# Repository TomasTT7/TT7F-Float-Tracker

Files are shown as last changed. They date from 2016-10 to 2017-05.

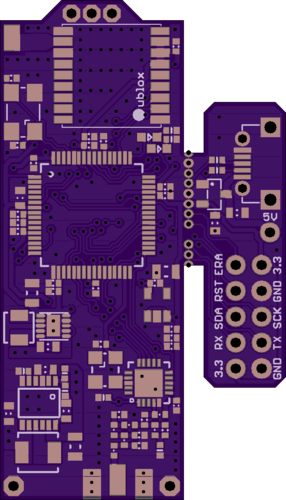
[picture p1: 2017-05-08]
Hardware/TT7F v1.5 top.png

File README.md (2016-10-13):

# TT7F-Float-Tracker

This is the main repository for [TT7F high altitude balloon tracker](http://tt7hab.blogspot.cz/2016/08/the-tt7f-hardware.html).
It includes the board and schematic Eagle files and the current state of software that is continually being worked on.

The tracker is designed around Atmel's SAM3S8B microcontroller. It acquires the current position from Ublox MAX-M8Q GPS module. As a transmitter it uses Silicon Labs Si4060 to transmit in the 70cm and 2m bands. It is also equipped with a connector and an interface for MT9D111 camera module to provide [SSDV](https://ukhas.org.uk/guides:ssdv) (Slow Scan Digital Video) capability.

The power supply consists of TPS63031 buck-boost converter providing 3.3V to the MCU, GPS module and transmitter. The MT9D111 camera module is powered by two ME6211 LDO regulators (1.8V and 2.8V). The tracker is also capable of using LTC3105 MPPC converter in connection with a pair of solar cells to charge a battery (up to 4.2V) and power the TPS63031 converter.

For programming purposes it is equipped with a USB micro B interface which can provide power to the board via MCP1700 LDO regulator as well.

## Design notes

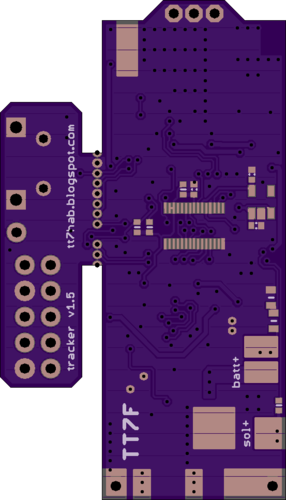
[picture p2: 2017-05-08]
Hardware/TT7F v1.5 bottom.png

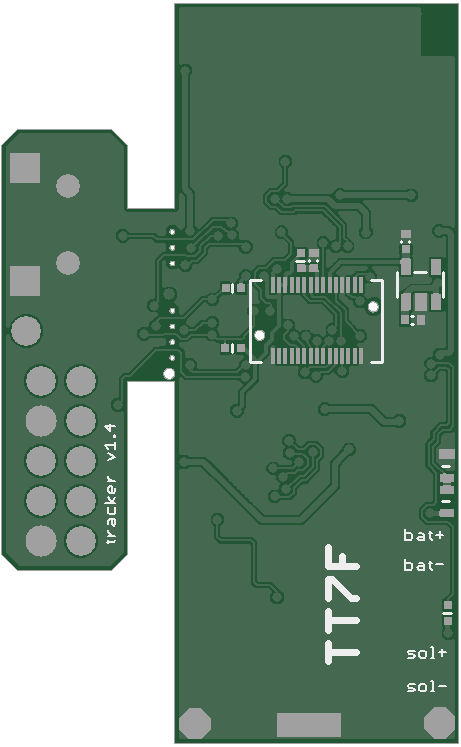
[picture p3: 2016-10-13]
Hardware/PCB bottom.png

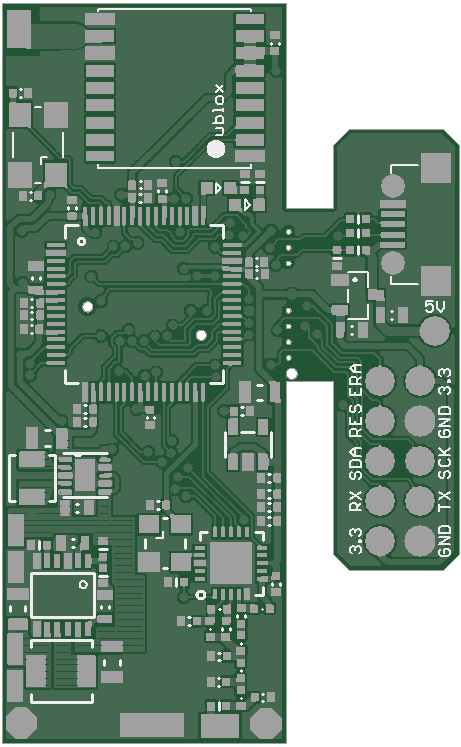
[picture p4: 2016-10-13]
Hardware/PCB top.png

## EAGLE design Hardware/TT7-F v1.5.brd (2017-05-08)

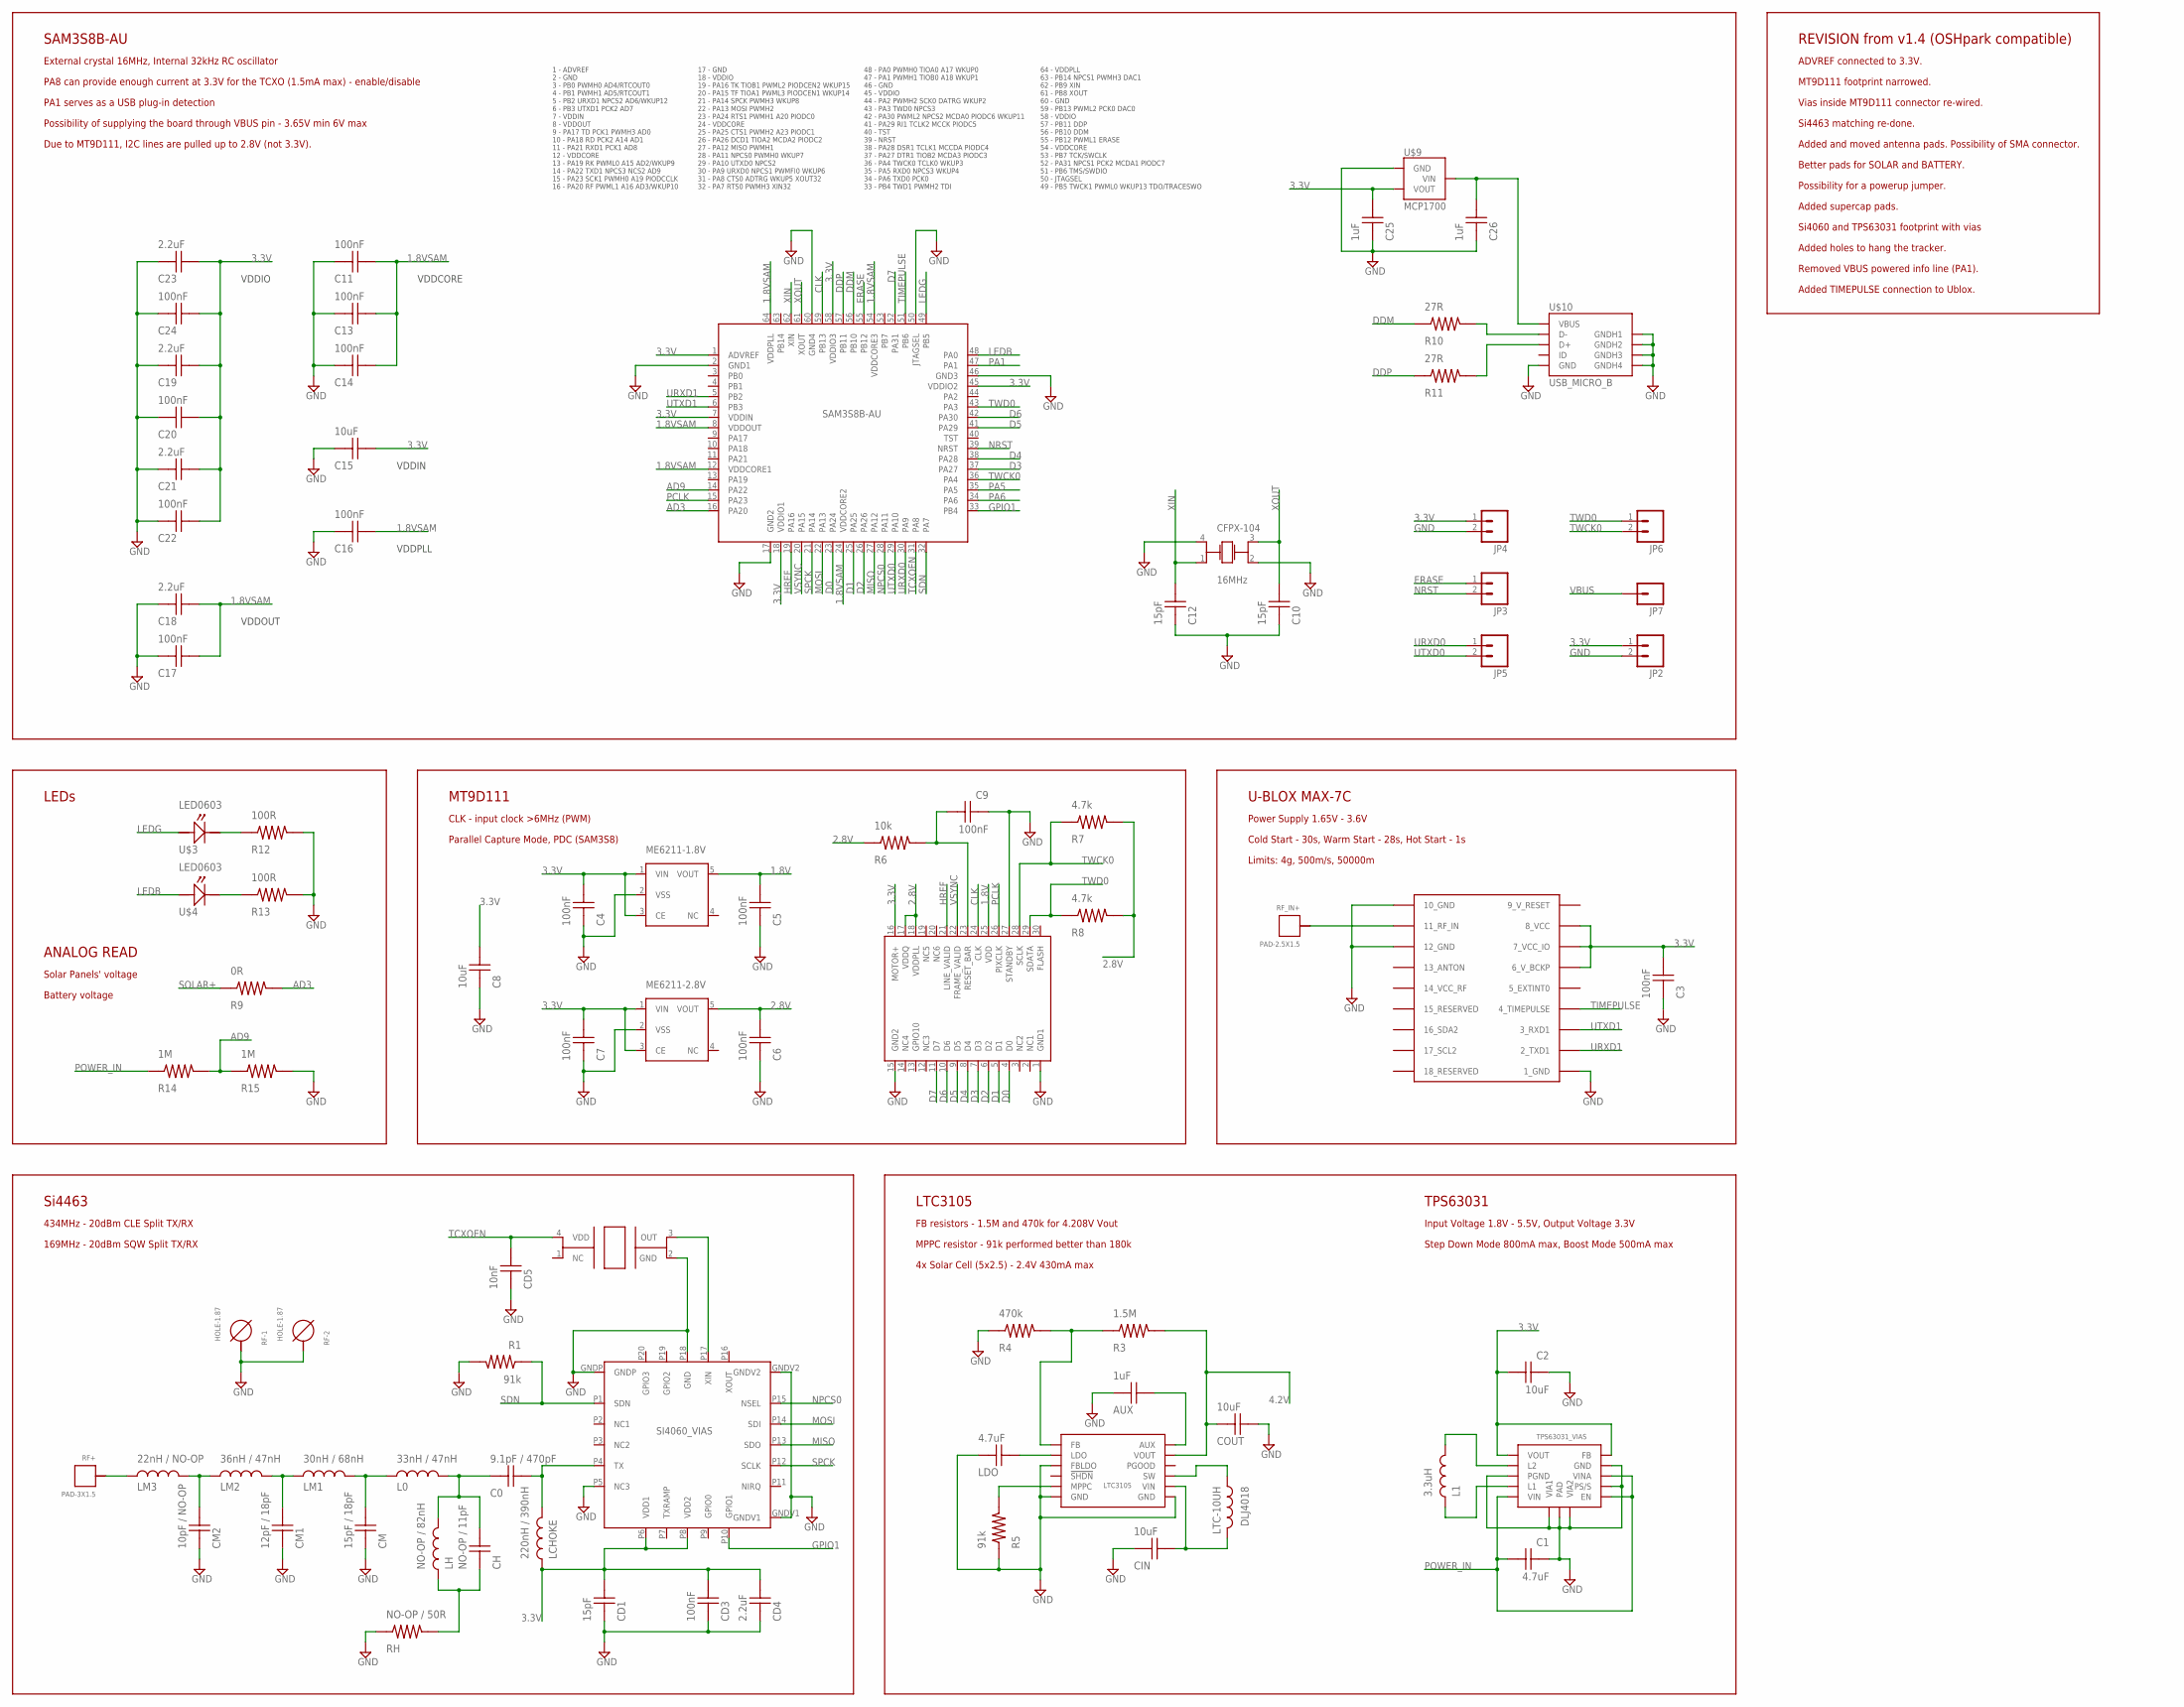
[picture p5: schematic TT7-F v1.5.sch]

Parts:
AUX: 1uF; CAP0603
C0: 9.1pF / 470pF; CAP0402
C1: 4.7uF; CAP0603
C2, C8: 10uF; CAP0805
C3, C4, C5, C6, C7, C9, C11, C13, C14, C16, C17, C20, C22, C24: 100nF; CAP0402
C10, C12: 15pF; CAP0402
C15: 10uF; CAP0603
C18, C19, C21, C23: 2.2uF; CAP0402
C25, C26: 1uF; CAP0603
CD1: 15pF; CAP0402
CD3: 100nF; CAP0402
CD4: 2.2uF; CAP0402
CD5: 10nF; CAP0402
CFPX-104: 16MHz; CFPX-104
CH: NO-OP / 11pF; CAP0402
CIN: 10uF; CAP0603
CM: 15pF / 18pF; CAP0402
CM1: 12pF / 18pF; CAP0402
CM2: 10pF / NO-OP; CAP0402
COUT: 10uF; CAP0805
JP2, JP3, JP4, JP5, JP6: M021X02_NO_SILK; 1X02_NO_SILK
JP7: M01PTH_NO_SILK_YES_STOP; 1X01_NO_SILK
L0: 33nH / 47nH; IND0402
L1: 3.3uH; DLJ3015
LCHOKE: 220nH / 390nH; IND0402
LDO: 4.7uF; CAP0603
LH: NO-OP / 82nH; IND0402
LM1: 30nH / 68nH; IND0402
LM2: 36nH / 47nH; IND0402
LM3: 22nH / NO-OP; IND0402
LTC-10UH: DLJ4018
ME6211-1.8V, ME6211-2.8V: ME6211_NEW
R1, R5: 91k; RES0402
R3: 1.5M; RES0402
R4: 470k; RES0402
R6: 10k; RES0402
R7, R8: 4.7k; RES0402
R9: 0R; RES0402
R10, R11: 27R; RES0402
R12, R13: 100R; RES0402
R14, R15: 1M; RES0603
RF+: PAD-3X1.5
RF-1, RF-2: HOLE-1.87
RF_IN+: PAD-2.5X1.5
RH: NO-OP / 50R; RES0402
TCXO: 32MHz; I547-2P3_TCXO
U1: LTC3105
U3: TPS63031_VIAS
U4: SAM3S8B-AU
U$1: SI4060_VIAS
U$2: UBLOX_MAX-7C
U$3, U$4: LED0603
U$9: MCP1700
U$10: USB_MICRO_B
U$15: MT9D111-AVX145602-NEW

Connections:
1.8V: C5.P$2, ME6211-1.8V.5 (VOUT), U$15.25 (VDD)
1.8VSAM: C11.P$2, C13.P$2, C14.P$2, C16.P$2, C17.P$2, C18.P$2, U4.8 (VDDOUT), U4.12 (VDDCORE1), U4.24 (VDDCORE2), U4.54 (VDDCORE3), U4.64 (VDDPLL)
2.8V: C6.P$2, ME6211-2.8V.5 (VOUT), R6.P$1, R7.P$2, R8.P$2, U$15.17 (VDDQ), U$15.18 (VDDPLL)
3.3V: C2.P$2, C3.P$2, C4.P$2, C7.P$2, C8.P$2, C15.P$2, C19.P$2, C20.P$2, C21.P$2, C22.P$2, C23.P$2, C24.P$2, C25.P$2, CD1.P$2, CD3.P$2, CD4.P$2, JP2.1, JP4.1, LCHOKE.P$1, ME6211-1.8V.1 (VIN), ME6211-1.8V.3 (CE), ME6211-2.8V.1 (VIN), ME6211-2.8V.3 (CE), U3.1 (VOUT), U3.10 (FB), U4.1 (ADVREF), U4.7 (VDDIN), U4.18 (VDDIO1), U4.45 (VDDIO2), U4.58 (VDDIO3), U$1.P6 (VDD1), U$1.P8 (VDD2), U$2.6_V_BCKP, U$2.7_VCC_IO, U$2.8_VCC, U$9.2 (VOUT), U$15.16 (MOTOR+)
4.2V: COUT.P$1, R3.P$2, U1.11 (VOUT)
9_V_RESET: U$2.9_V_RESET
AD3: R9.P$2, U4.16 (PA20)
AD9: R14.P$2, R15.P$1, U4.14 (PA22)
CLK: U4.59 (PB13), U$15.24 (CLK)
D0: U4.23 (PA24), U$15.4 (D0)
D1: U4.25 (PA25), U$15.5 (D1)
D2: U4.26 (PA26), U$15.6 (D2)
D3: U4.37 (PA27), U$15.7 (D3)
D4: U4.38 (PA28), U$15.8 (D4)
D5: U4.41 (PA29), U$15.9 (D5)
D6: U4.42 (PA30), U$15.10 (D6)
D7: U4.52 (PA31), U$15.11 (D7)
DDM: R10.P$1, U4.56 (PB10)
DDP: R11.P$1, U4.57 (PB11)
ERASE: JP3.1, U4.55 (PB12)
GND: AUX.P$1, C1.P$1, C2.P$1, C3.P$1, C4.P$1, C5.P$1, C6.P$1, C7.P$1, C8.P$1, C9.P$1, C10.P$1, C11.P$1, C12.P$1, C13.P$1, C14.P$1, C15.P$1, C16.P$1, C17.P$1, C18.P$1, C19.P$1, C20.P$1, C21.P$1, C22.P$1, C23.P$1, C24.P$1, C25.P$1, C26.P$1, CD1.P$1, CD3.P$1, CD4.P$1, CD5.P$1, CFPX-104.2 (GND1), CFPX-104.4 (GND2), CIN.P$1, CM.P$1, CM1.P$1, CM2.P$1, COUT.P$2, JP2.2, JP4.2, LDO.P$1, ME6211-1.8V.2 (VSS), ME6211-2.8V.2 (VSS), R1.P$2, R4.P$1, R5.P$1, R12.P$2, R13.P$2, R15.P$2, RF-1.P$1, RF-2.P$1, RH.P$1, TCXO.2 (GND), U1.3 (FBLDO), U1.6 (GND), U1.7 (GND), U3.3 (PGND), U3.7 (PS/S), U3.9 (GND), U3.11 (PAD), U3.VIA1, U3.VIA2, U4.2 (GND1), U4.17 (GND2), U4.46 (GND3), U4.50 (JTAGSEL), U4.60 (GND4), U$1.GNDP, U$1.GNDV1, U$1.GNDV2, U$1.P5 (NC3), U$1.P18 (GND), U$2.1_GND, U$2.10_GND, U$2.12_GND, U$9.1 (GND), U$10.GND, U$10.P$6 (GNDH1), U$10.P$7 (GNDH2), U$10.P$8 (GNDH3), U$10.P$9 (GNDH4), U$15.1 (GND1), U$15.15 (GND2), U$15.27 (STANDBY)
GPIO1: U4.33 (PB4), U$1.P10 (GPIO1)
HREF: U4.19 (PA16), U$15.21 (LINE_VALID)
LEDB: U4.48 (PA0), U$4.ANODE
LEDG: U4.49 (PB5), U$3.ANODE
MISO: U4.27 (PA12), U$1.P13 (SDO)
MOSI: U4.22 (PA13), U$1.P14 (SDI)
unnamed: CH.P$1, LH.P$1, RH.P$2
unnamed: C0.P$2, LCHOKE.P$2, U$1.P4 (TX)
unnamed: R12.P$1, U$3.CATHODE
unnamed: C0.P$1, CH.P$2, L0.P$2, LH.P$2
unnamed: CM.P$2, L0.P$1, LM1.P$2
unnamed: CM1.P$2, LM1.P$1, LM2.P$2
unnamed: CM2.P$2, LM2.P$1, LM3.P$2
unnamed: TCXO.3 (OUT), U$1.P17 (XIN)
unnamed: L1.P$1, U3.4 (L1)
unnamed: LTC-10UH.P$1, U1.9 (SW)
unnamed: LM3.P$1, RF+.P$1
unnamed: LDO.P$2, U1.2 (LDO)
unnamed: R5.P$2, U1.5 (MPPC)
unnamed: AUX.P$2, U1.12 (AUX)
unnamed: L1.P$2, U3.2 (L2)
unnamed: R3.P$1, R4.P$2, U1.1 (FB)
unnamed: RF_IN+.P$1, U$2.11_RF_IN
unnamed: R11.P$2, U$10.D+
unnamed: R10.P$2, U$10.D-
unnamed: C9.P$2, R6.P$2, U$15.23 (RESET_BAR)
unnamed: R13.P$1, U$4.CATHODE
NPCS0: U4.28 (PA11), U$1.P15 (NSEL)
NRST: JP3.2, U4.39 (NRST)
PA1: U4.47 (PA1)
PA5: U4.35 (PA5)
PA6: U4.34 (PA6)
PCLK: U4.15 (PA23), U$15.26 (PIXCLK)
POWER_IN: C1.P$2, R14.P$1, U3.5 (VIN), U3.6 (EN), U3.8 (VINA)
SDN: R1.P$1, U4.32 (PA7), U$1.P1 (SDN)
SOLAR+: CIN.P$2, LTC-10UH.P$2, R9.P$1, U1.8 (VIN)
SPCK: U4.21 (PA14), U$1.P12 (SCLK)
TCXOEN: CD5.P$2, TCXO.4 (VDD), U4.31 (PA8)
TIMEPULSE: U4.51 (PB6), U$2.4_TIMEPULSE
TWCK0: JP6.2, R7.P$1, U4.36 (PA4), U$15.28 (SCLK)
TWD0: JP6.1, R8.P$1, U4.43 (PA3), U$15.29 (SDATA)
URXD0: JP5.1, U4.30 (PA9)
URXD1: U4.5 (PB2), U$2.2_TXD1
UTXD0: JP5.2, U4.29 (PA10)
UTXD1: U4.6 (PB3), U$2.3_RXD1
VBUS: C26.P$2, JP7.1, U$9.3 (VIN), U$10.VBUS
VSYNC: U4.20 (PA15), U$15.22 (FRAME_VALID)
XIN: C12.P$2, CFPX-104.1 (XTAL1), U4.62 (XIN)
XOUT: C10.P$2, CFPX-104.3 (XTAL2), U4.61 (XOUT)

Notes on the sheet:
Si4463
434MHz - 20dBm CLE Split TX/RX
LTC3105
TPS63031
FB resistors - 1.5M and 470k for 4.208V Vout
MPPC resistor - 91k performed better than 180k
4x Solar Cell (5x2.5) - 2.4V 430mA max
Input Voltage 1.8V - 5.5V, Output Voltage 3.3V
Step Down Mode 800mA max, Boost Mode 500mA max
U-BLOX MAX-7C
Power Supply 1.65V - 3.6V
Cold Start - 30s, Warm Start - 28s, Hot Start - 1s
Limits: 4g, 500m/s, 50000m
MT9D111
SAM3S8B-AU
CLK - input clock >6MHz (PWM)
Parallel Capture Mode, PDC (SAM3S8)
LEDs
ANALOG READ
External crystal 16MHz, Internal 32kHz RC oscillator
Solar Panels' voltage
Battery voltage
VDDIO
VDDCORE
VDDIN
VDDPLL
VDDOUT
PA8 can provide enough current at 3.3V for the TCXO (1.5mA max) - enable/disable
PA1 serves as a USB plug-in detection
Possibility of supplying the board through VBUS pin - 3.65V min 6V max
Due to MT9D111, I2C lines are pulled up to 2.8V (not 3.3V).
ADVREF connected to 3.3V.
REVISION from v1.4 (OSHpark compatible)
MT9D111 footprint narrowed.
Vias inside MT9D111 connector re-wired.
Si4463 matching re-done.
Added and moved antenna pads. Possibility of SMA connector.
Better pads for SOLAR and BATTERY.
Possibility for a powerup jumper.
169MHz - 20dBm SQW Split TX/RX

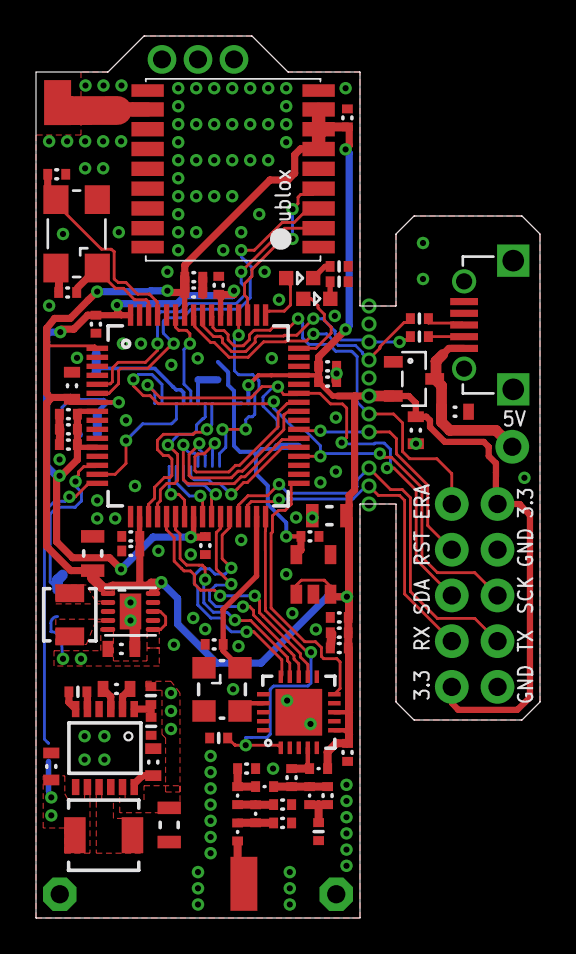
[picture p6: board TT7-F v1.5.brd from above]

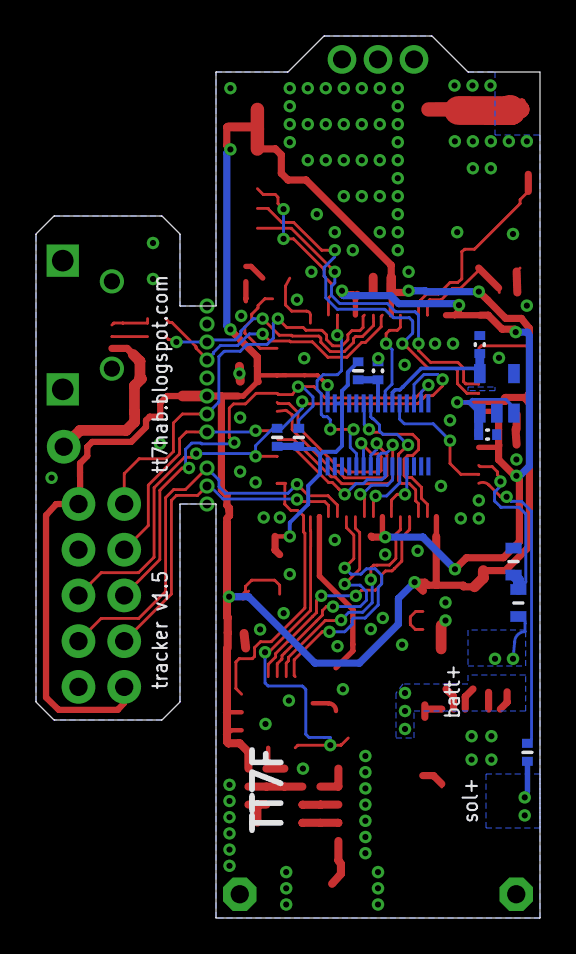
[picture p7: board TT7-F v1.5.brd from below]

Board: 2 copper layers, 28.0 x 49.0 mm, 86 parts (11 on the bottom side), 66 nets.

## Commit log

2016-10-13 Initial commit.
    [TT7-F v1.4.brd, TT7-F v1.4.sch]
2016-11-01 SPI cleaning.
2016-11-14 Better de-init.
2016-11-14 Calibrated offset.
2017-05-08 New version.
    [TT7-F v1.5.brd, TT7-F v1.5.sch]
2017-09-26 Updated a couple of borders.
2017-09-26 Updated a couple of area borders.
2017-09-26 UART communication timeout added.

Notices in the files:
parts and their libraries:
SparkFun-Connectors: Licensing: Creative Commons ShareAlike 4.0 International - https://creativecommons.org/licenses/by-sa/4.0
